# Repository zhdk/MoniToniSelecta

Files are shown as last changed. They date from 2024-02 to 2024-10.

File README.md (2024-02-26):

<h1>MoniToni Vending Machine Integration</h1>
Integration of ZHdK-Workshop Vending Machines into the MoniToni Payment System
<h2>Hardware</h2>
<h3>Electrical</h3>
<h3>Embedded Systems</h3>
Microcontroller: ESP32-S3 DevKitC by Esprssif <href>https://docs.espressif.com/projects/esp-idf/en/latest/esp32s3/hw-reference/esp32s3/user-guide-devkitc-1.html</href>
<h2>Setup</h2>
<h3>MAC-Address</h3>
Get specific MAC-Address of used ESP32-S3
<h3>WIFI</h3>
<h3>Hardware Tests</h3>
<h3>MoniToni-Terminal ID</h3>
<h3>TO-DO</h3>
<li>Generalized Item Amount</li>

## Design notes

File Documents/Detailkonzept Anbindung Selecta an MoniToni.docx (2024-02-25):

# Detailkonzept Anbindung Selecta an MoniToni

# 1. Ausbau der alten Komponenten

- Klimakompressor
- FL- Beleuchtung
- Kassensystem
- Printplatten
- Kühlaggregat
- Expansionsgefäss
- Ventilatoren
- Zahlterminal
- 10ner Tastatur
- Kassentresor
- Münzeinwurf

# 2. Einbau der Mechanischen und elektrischen Komponenten

## Einbau der elektronischen Steuereinheit im unteren Bereich der Türe und im Apparat, alle nicht genutzten Löcher werden verschlossen (Sicherheit)

- 1x Arduino mit WLAN
- 1x externe Antenne
- 2x Relaisboard (1x in der Türe, 1x im Automaten)
- 1x Schalter (Push) im Automaten (Befüllen)
- 1x Netzgerät 5V in der Türe (Arduino und Relaisboard
- 1x Netzgerät 24V in der Türe
- 1x USB-Ladegerät
- 2x 1.5m LED-Band für die Beleuchtung
- 1x Piezo (Fach- Summer, wenn Offen)
- 10x Grüne LED, wenn Ready zum Materialkauf (Türe entriegelt)
- 1x Relais für Motor
- 1x DIN-Schiene
- 1x Feinsicherung DIN-Schiene 5V (A unbekannt)
- 1x Feinsicherung DIN-Schiene 24V (A unbekannt)
- 1x Ventilator 5V oder 24V
- 1x Zuluftgitter
- 1x Apparatesteckdose

# 3. Beschriftung des Apparates und Funktionen

- Preise (pro Etage)
- QR-Code (pro Etage)
- Wahlselektor= Push&Hold

# 4. Funktion der Mechanik

- 1. Inhouse Schalter, um die Trommeln zu drehen (Befüllen)
- 2. Gelber Knopf Push -> Wakeup (Licht, Wlan connection Ja/Nein, Gelber Knopf leuchtet, wenn Gerät Ready)
- 3. Gelber Knopf Hold -> Produktewahl (alle Ebenen entsperren, Relais in Serie), Trommelmotor läuft nach 0.5 sec. Verzögerung zu den Relais)
- 4. Wenn gelber Knop losgelassen wird = Motor Stopp -> alle Ebenen sperren, Motor läuft 3 sec. weiter
- 5. QR von gewünschter Produktebene scannen -> wenn Kauf bewilligt wird, türfachfach der Ebene wird freigeschaltet, freigeschaltete Ebene wird optisch angezeigt (LED) Motor kann nicht gedreht werden.
- 6. Warenbezug -> Türe wird aufgeschoben, Schalter Zustand Türe offen (Summer (Delay 5 Sek.) ertönt so lange wie Türschalter offen, MoniToni wird abgerechnet)
- 7. Türe schliessen -> Türschalter schliesst, Summer stumm, Türe wird verriegelt
- Gerätestatus wie 3.
- 8. Sleep Mode -> nach 5 Minuten

# 5. Programmierung Arduino

## Input

- Gelber Knopf, aufwecken, Gelber Knopf gedrückt halten, Trommelrelais (in Serie) freischalten, nach 0.5 sec. Motorstart bis zum gewünschten Produkt, gelber Knopf loslassen, Relais stromlos (sperren), 3 sec. Motornachlaufachlauf
- Fächerschalter (in Serie)
- QR von gewünschter Produktebene scannen -> wenn Kauf bewilligt, Türfachfach der Ebene wird freigeschaltet, freigeschaltete Ebene wird optisch angezeigt (grün LED)
- Warenbezug -> Türe wird aufgeschoben, MoniToni wird abgerechnet) Schalter Zustand Türe offen Signal an Arduino (Summer Delay 5 Sek. ertönt so lange wie Türschalter offen,

## Output

- 1x Ebenen freischalten (Trommelrelais in Serie)
- Motor Steuerung
- 10x Fächerrelais steuern für den Verkauf
- LED-Beleuchtung
- Piezo (Summer)
- 10x grüne LED`s

# 6. Cubera

- Maschine erstellen
- Produkte erstellen
- Preise anpassen
- Auswertung jeder einzelnen Maschine (Geldfluss)

# 7. Test-Cases

- Systemtest Mechanisch
- Regressionstest ganzes MoniToni

# 8. Bestellliste für 4 Automaten

- 4x Arduino mit WLAN (Muss noch genau eruiert werden welches)
- 4x Externe Antenne
- 8x Relaisboard
- 4x Schalter (Pushbutton)
- 4x Netzgerät 5V
- 4x Netzgerät 24V
- 16m LED Band Beleuchtung
- 4x Piezo für offene Schublade
- 40x grüne LED für Schublade offen
- 4x Relais 24V/230V Motor
- 4x Apparatesteckdose 230V
- 4x 30cm DIN-Schiene für Elektroinstallationen
- 4x Feinsicherung DIN-Schiene 5V (A unbekannt)
- 4x Feinsicherung DIN-Schiene 24V (A unbekannt)
- Mehradriges Kabel
- 2x USB-Ladegerät
- 4x Ventilator 5V oder 24V
- 4x Zuluftgitter

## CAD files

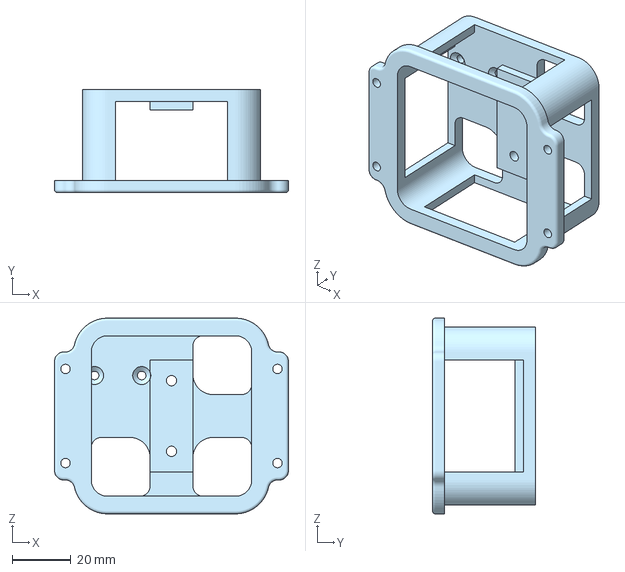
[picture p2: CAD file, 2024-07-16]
Hardware/3D-Print/M5CoreS3 Panel Front Mount Frame.3mf
79.5 x 35.0 x 66.5 mm

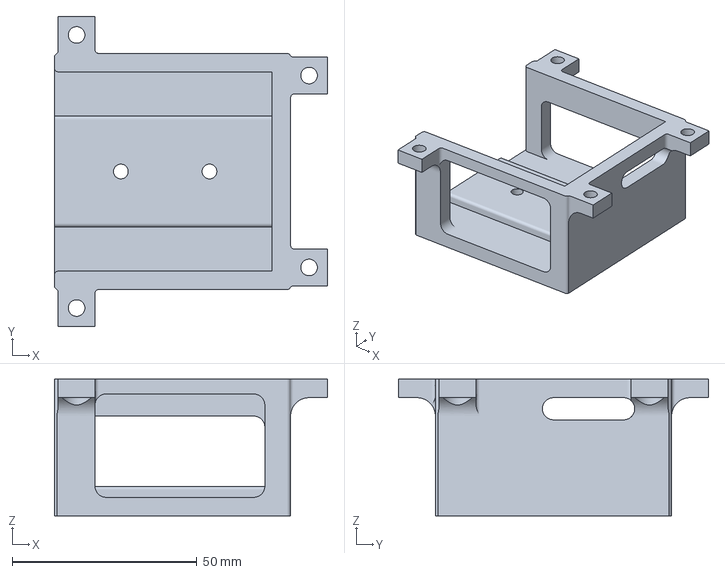
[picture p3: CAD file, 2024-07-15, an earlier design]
Hardware/3D-Print/Legacy/M5CoreS3 Mounting Frame.3mf
74.0 x 84.0 x 37.0 mm

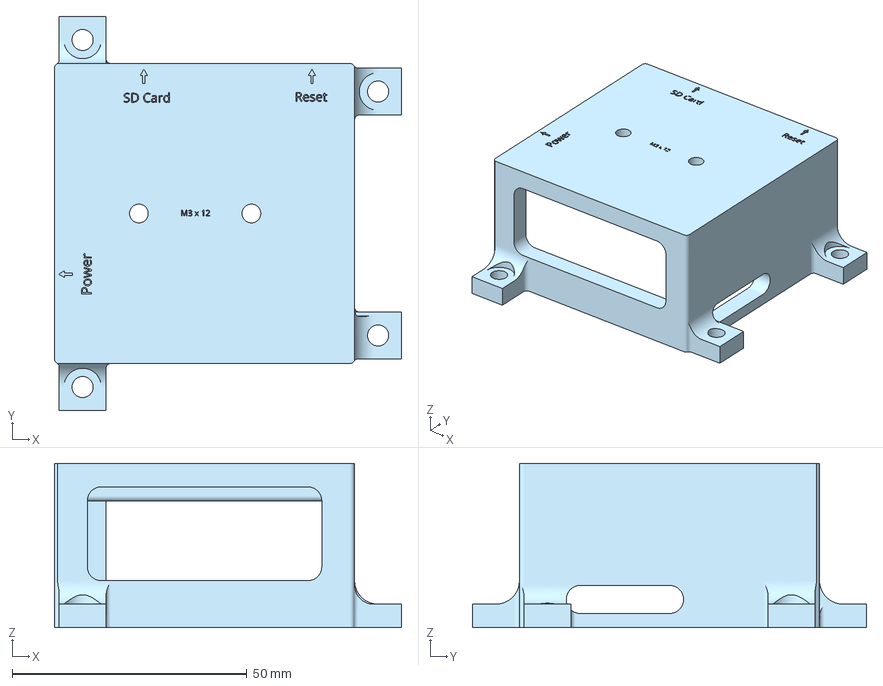
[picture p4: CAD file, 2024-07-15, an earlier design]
Hardware/3D-Print/Legacy/M5CoreS3 Mounting Frame - Display Offset.3mf
74.0 x 84.0 x 35.0 mm

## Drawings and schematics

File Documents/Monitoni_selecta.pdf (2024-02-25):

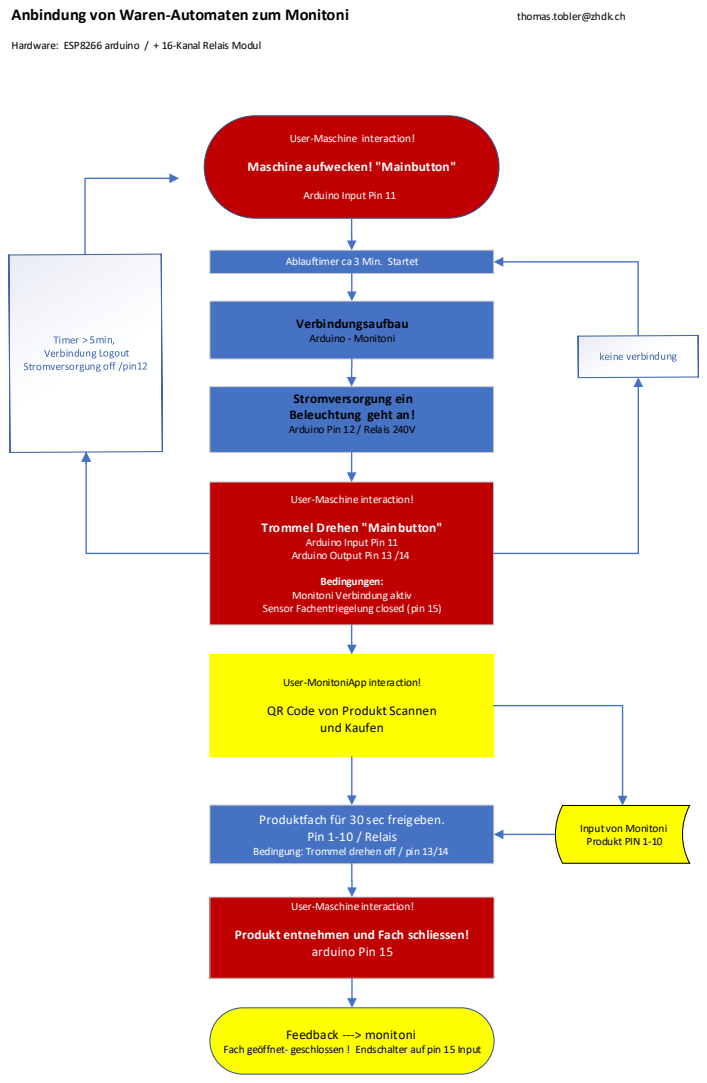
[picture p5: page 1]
Verbindungsaufbau Arduino - Monitoni; und Kaufen; Pin 1-10 / Relais; arduino Pin 15; Feedback ---> monitoni; Anbindung von Waren-Automaten zum Monitoni; thomas.tobler@zhdk.ch

Hardware: ESP8266 arduino / + 16-Kanal Relais Modul

User-Maschine interaction!

Maschine aufwecken! "Mainbutton"

Arduino Input Pin 11

Ablauftimer ca 3 Min. Startet

Stromversorgung ein
Beleuchtung geht an!
Arduino Pin 12 / Relais 240V

Trommel Drehen "Mainbutton"

Arduino Output Pin 13 /14

Bedingungen:
Monitoni Verbindung aktiv
Sensor Fachentriegelung closed (pin 15)

User-MonitoniApp interaction!

QR Code von Produkt Scannen

Produktfach für 30 sec freigeben.

Input von Monitoni
Produkt PIN 1-10

Bedingung: Trommel drehen off / pin 13/14

Produkt entnehmen und Fach schliessen!

Fach geöffnet- geschlossen ! Endschalter auf pin 15 Input

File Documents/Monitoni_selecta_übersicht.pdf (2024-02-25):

1)

## Selecta-

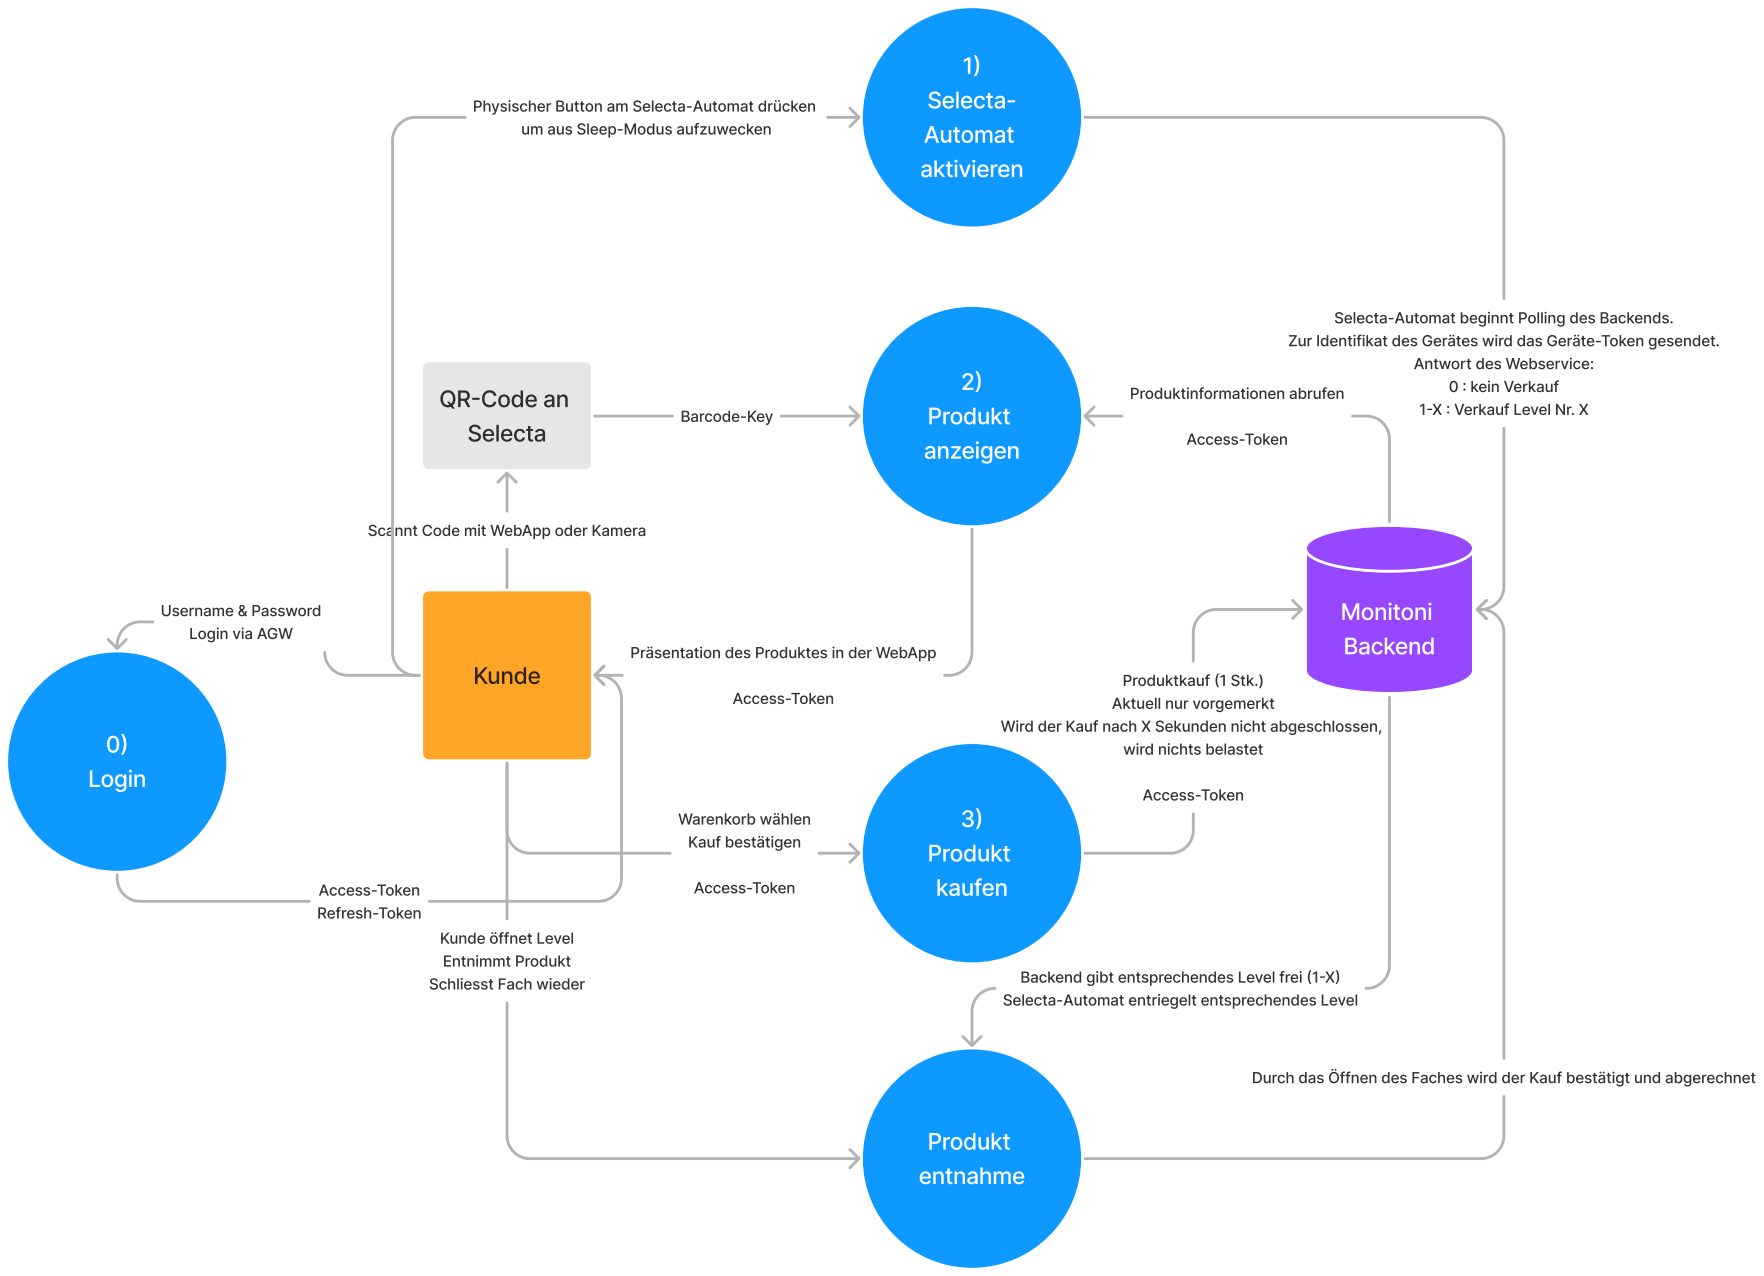
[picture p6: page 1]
Selecta; Produkt; anzeigen; Barcode-Key; Monitoni; Backend; Produktinformationen abrufen; Access-Token; Kunde; kaufen; Warenkorb wählen; Kauf bestätigen; Produktkauf (1 Stk.); Automat; aktivieren; 0 : kein Verkauf; entnahme; öffnet Leve l; Entnimmt Produkt; Schliesst; Fach wieder; Durch das; Öffnen des; Login; & Passwor d; Access-Toke n; Refresh-Token

Physischer Button am Selecta-Automat drücken

um aus Sleep-Modus aufzuwecken

Selecta-Automat beginnt Polling des Backends.

Zur Identifikat des Gerätes wird das Geräte-Token gesendet.

Antwort des Webservice:

QR-Code an

1-X : Verkauf Level Nr. X

Scannt Code mit WebApp oder Kamera

Username
Login via AGW

Präsentation des Produktes in der WebApp

Aktuell nur vorgemerkt

Wird der Kauf nach X Sekunden nicht abgeschlossen,

wird nichts belastet

Backend gibt entsprechendes Level frei (1-X)

Selecta-Automat entriegelt entsprechendes Level

Faches wird der Kauf bestätigt und abgerechnet

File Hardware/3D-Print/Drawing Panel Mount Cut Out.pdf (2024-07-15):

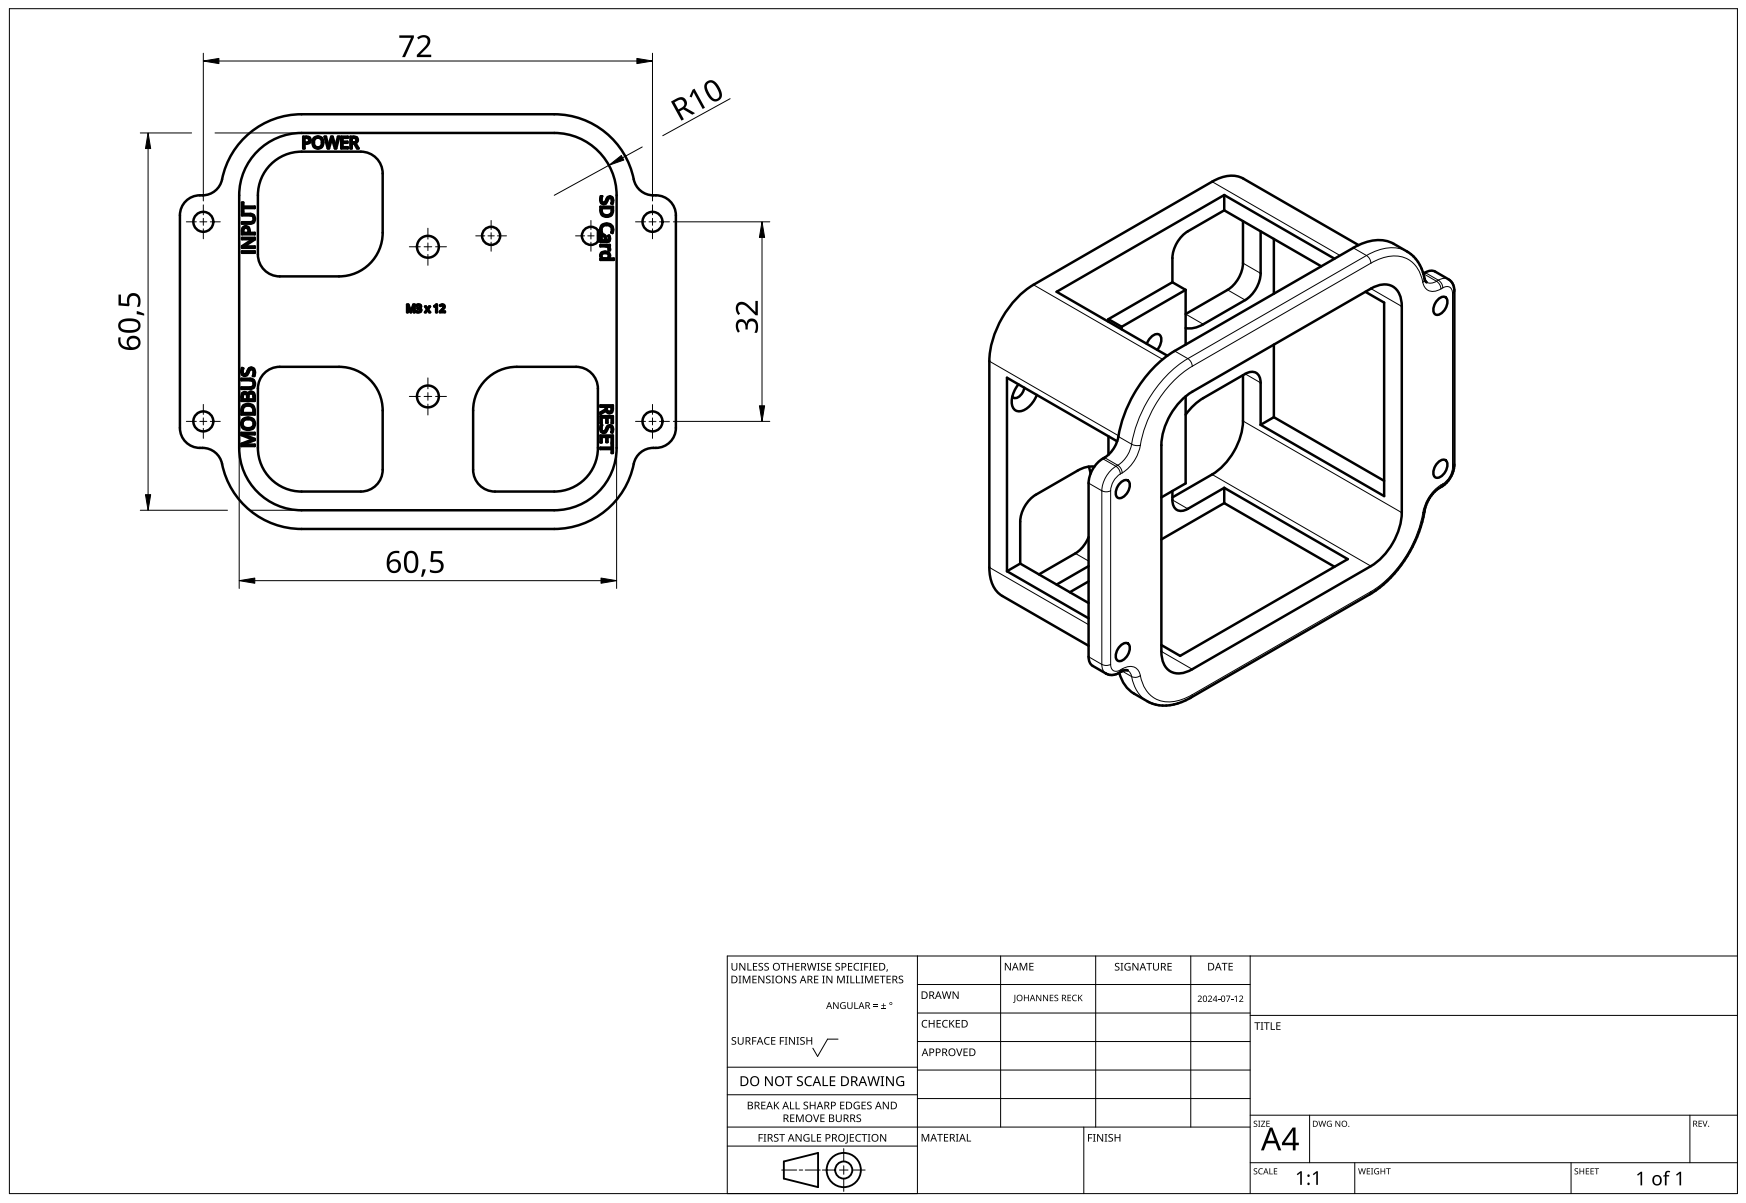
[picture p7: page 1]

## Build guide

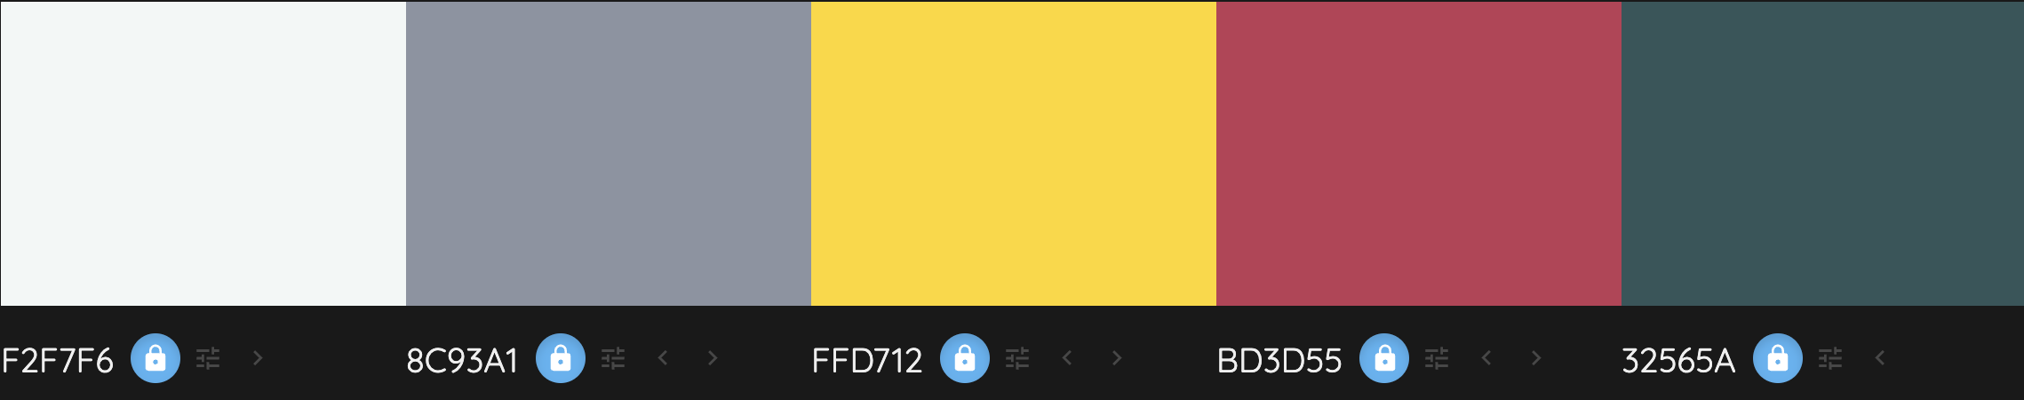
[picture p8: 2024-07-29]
UI/Color Guide/Illustrator/MoniToni Color Palette.png

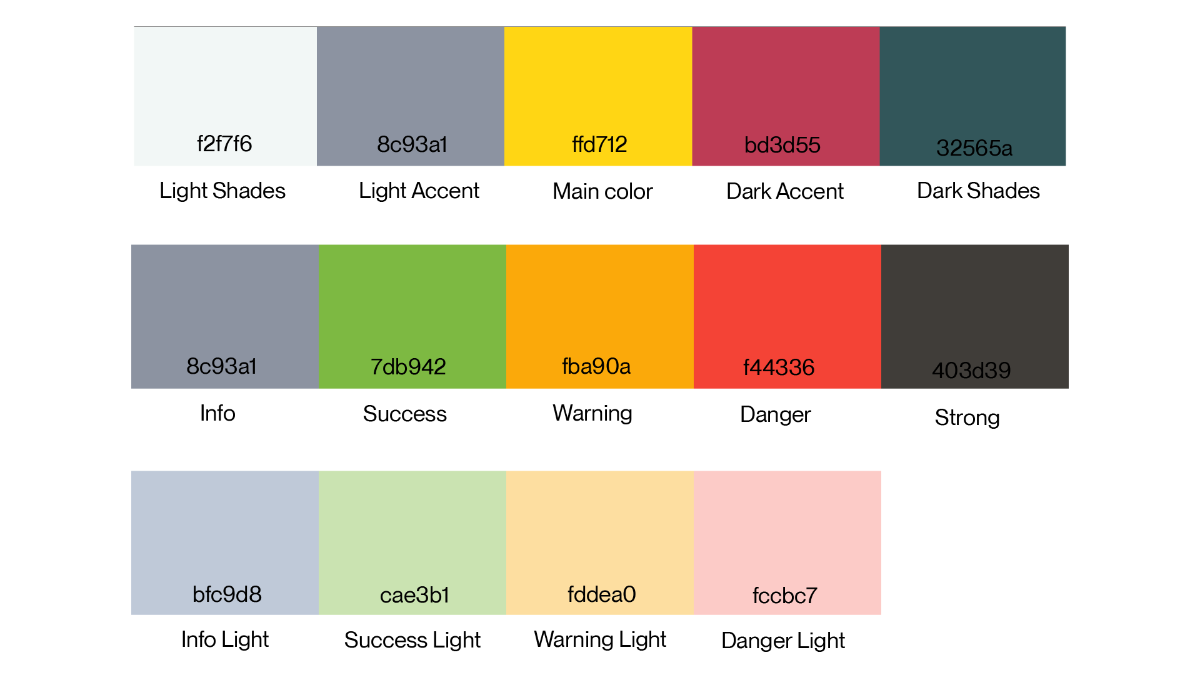
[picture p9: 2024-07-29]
UI/Color Guide/Codes.png

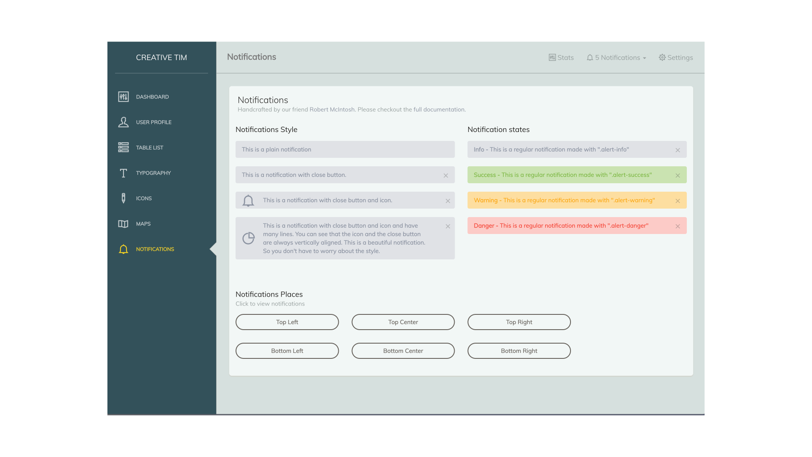
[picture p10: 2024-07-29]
UI/Color Guide/Example.png

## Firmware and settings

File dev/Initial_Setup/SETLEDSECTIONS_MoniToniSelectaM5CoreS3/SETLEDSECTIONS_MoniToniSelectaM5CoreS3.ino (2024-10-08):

// _____________MoniToni Vending Machine Integration_____________
// Hardware Iteration: M5CoreS3 Microcontroller & Waveshare 32CH Modbus RTU Relay Board



// _____________definitions_____________
// Debugger
// define DEBUGLOG_ENABLE_FILE_LOGGER to enable file logger
#define DEBUGLOG_ENABLE_FILE_LOGGER

// set log level NONE, ERROR, WARN, INFO, DEBUG, TRACE
#define DEBUGLOG_DEFAULT_LOG_LEVEL_DEBUG

// set log level for file output NONE, ERROR, WARN, INFO, DEBUG, TRACE
#define DEBUGLOG_DEFAULT_FILE_LEVEL_TRACE

// choose one of the two debug preambles
// default preamble with file & codeline information about debug source
//  #define LOG_PREAMBLE LOG_SHORT_FILENAME, LOG_MACRO_APPEND_STR(L.__LINE__), __func__, ":"
// no preamble
#define LOG_PREAMBLE ""

// Uncommenting DEBUGLOG_DISABLE_LOG disables ASSERT and all log (Release Mode)
// PRINT and PRINTLN are always valid even in Release Mode
// #define DEBUGLOG_DISABLE_LOG


// SD Card
#define SD_SPI_SCK_PIN  36
#define SD_SPI_MISO_PIN 35
#define SD_SPI_MOSI_PIN 37
#define SD_SPI_CS_PIN   4

// SERIAL2 PINS M5CoreS3
#define RX_PIN_SERIAL2 18
#define TX_PIN_SERIAL2 17

// PINS IN
// #define Door_PIN 8   //GPIO 8 - M5CoreS3
// #define ButtonTurn_PIN 48 
// #define ButtonOpen_PIN 21 

// RELAY CONFIG
#define Item_1_CH 1  //Relay 1
#define Item_2_CH 2  //Relay 2
#define Item_3_CH 3  //Relay 3
#define Item_4_CH 4  //Relay 4
#define Item_5_CH 5  //Relay 5
#define Item_6_CH 6  //Relay 6
#define Item_7_CH 7  //Relay 7
#define Item_8_CH 8  //Relay 8 
#define Item_9_CH 9  //Relay 9
#define Item_10_CH 10  //Relay 10
#define Light_CH 11  //Relay 11
#define Lock_CH 12  //Relay 12
#define Sirene_CH 13  //Relay 13
#define Motor_CH 14  //Relay 14
#define Relay15_CH 15  //Relay 15
#define Relay16_CH 16  //Relay 16
// #define Error_PIN 47 //Yellow


// Delays (in microseconds)
// #define CarrouselDELAY 100
#define CarrouselDELAY 0
#define UserInputDELAY 5000
#define SleepDELAY 120000
#define debounceTurnButton 1
#define debounceOpenButton 1
#define debounceDoor 10
#define openDoorDELAY 500
#define PurchaseTimeoutDELAY 60000
#define DoorOpenSireneDELAY 10000
#define ServerTimeout 3000
#define MotorTurnDELAY 2400
#define BluetoothSetupDelay 15000
#define ErrorDELAY 3000


// Proximity Sensor
#define ProximityThreshold 3


// Speaker Volume [0 - 255]
#define SpeakerVolume 60
// Speaker Frequency [in Hz]
#define SpeakerFrequency 1000


// Graphics
// Display Brightness [0 - 100]
#define TFT_BRIGHTNESS 90
// Screen Resolution
#define TFT_HOR_RES   240
#define TFT_VER_RES   320

/*LVGL draw into this buffer, 1/10 screen size usually works well. The size is in bytes*/
// #define DRAW_BUF_SIZE (TFT_HOR_RES * TFT_VER_RES / 10 * (LV_COLOR_DEPTH / 8))
#define DRAW_BUF_SIZE (TFT_HOR_RES * TFT_VER_RES / 8 * (LV_COLOR_DEPTH / 8))
//uint32_t draw_buf[DRAW_BUF_SIZE / 4];

#define READINGDELAY 8000

// LED Hub Port
#define CONNECTEDHUBPORT 0

// LED PIXEL COUNT
#define LED_PIN 9

// LED PIXEL COUNT
#define NUMPIXELS 172

// LED BRIGHTNESS [0 - 255]
#define BRIGHTNESS 255

// LED BLINKRATE
#define BLINKRATE 500

// LED MAPPING
#define LED_LEVEL_1_START 0
#define LED_LEVEL_1_END 17
#define LED_LEVEL_2_START 18
#define LED_LEVEL_2_END 34
#define LED_LEVEL_3_START 35
#define LED_LEVEL_3_END 51
#define LED_LEVEL_4_START 52
#define LED_LEVEL_4_END 68
#define LED_LEVEL_5_START 69
#define LED_LEVEL_5_END 85
#define LED_LEVEL_6_START 86
#define LED_LEVEL_6_END 103
#define LED_LEVEL_7_START 104
#define LED_LEVEL_7_END 120
#define LED_LEVEL_8_START 121
#define LED_LEVEL_8_END 137
#define LED_LEVEL_9_START 138
#define LED_LEVEL_9_END 154
#define LED_LEVEL_10_START 155
#define LED_LEVEL_10_END 172





// _____________Library Imports_____________

// M5CoreS3.h Libary by Tinyu-Zhao,M5Stack [1.0.0]
#include <M5CoreS3.h>

// Timer.h by Stefan Staub [1.2.1]
#include <Timer.h>

// ArduinoJson.h by Benoit Blanchon [7.0.3]
#include <ArduinoJson.h>

// SPI.h by Arduino [2.1.1] (Arduino IDE Version)
#include <SPI.h>

// WiFiClientSecure.h by Espressif Systems [2.0.11] (esp32 Boards Version)
#include <WiFiClientSecure.h>

// Wire.h for PBHUB I2C Communication
#include <Wire.h>

// debounce.h by Aaron Kimball [0.2.0]
#include <debounce.h>

// SD.h by Arduino, SparkFun [1.2.4]
#include <SD.h>

// DebugLog.h by hideakitai [0.8.3]
#include <DebugLog.h>

// Modbus Checksum Calculation
#include "modbus_crc.h"

// lvgl UI library [CUSTOM CONFIG & MODIFIED TFT_eSPI DRIVER]
#include <lvgl.h> 

// TFT display library [CUSTOM CONFIG]
#include <TFT_eSPI.h>

// UI Files [CUSTOM UI Files]
#include <ui.h>

// Credentials File
#include "credentials.h"

// // PBHUB Class
// #include "porthub.h"

// PBHUB, M5 [1.0.0]
#include <M5UnitPbHub.h>

#include <Adafruit_NeoPixel.h>

// _____________variables_____________

// Logic Variables
volatile int vendingState = 1; // 0 = Sleep, 1 = Idle, 2 = Turn, 3 = Validate, 4 = Collect, 5 = Finished, 6 = Error

volatile int activeScreen = 0; //  0 = StartUpScreen, 1 = MainScreen, 2 = ValidationScreen, 3 = EndScreen, 4 = SleepScreen, 5 = ErrorScreen

volatile int item;

volatile bool doorOpenState = false;
volatile bool buttonTurnPushedState = false;
volatile bool buttonOpenPushedState = false;
volatile bool carrouselUnlockedState = false;
volatile bool motorOnState = false;
volatile bool itemUnlockedState = false;
volatile bool sireneOnState = false;
volatile bool lightOnState = false;
volatile bool errorOnState = false;
volatile bool transactionActive = false;
volatile bool requestActive = false;
volatile bool proximityTriggered = false;
volatile bool displayOn = true;

// Network Variables
const char *SSID = WIFI_SSID;        // Change this to your WiFi SSID
const char *PW = WIFI_PASS; // Change this to your WiFi password
volatile bool wifiError = false;


const String host = "monitoni.zhdk.ch";
const int port = 443;

String url_permission = "/api/vending/permission";
String url_complete = "/api/vending/complete";
String url_close = "/api/vending/close";
String monitoni_terminal = TOKEN;

volatile bool permission = false;
volatile bool completed = false;
volatile bool closed = false;

volatile int globalHour;
volatile int globalMinute;
struct tm timeinfo;
time_t now;

void *draw_buf_1;                     // Draw Buffer for Graphics
unsigned long lastTickMillis = 0;   // Tick Variable for
lv_display_t * disp;                //display instance

uint16_t read_ps_value;   // Porximity Sensor Value

// PortHub porthub;  // PBHUB Instance
M5UnitPbHub pbhub;

// Pixel Instance - set number of LEDs, pin number, LED type.
Adafruit_NeoPixel LedPixels = Adafruit_NeoPixel(
    NUMPIXELS, LED_PIN,
    NEO_RGB + NEO_KHZ800);  


const int LEDMAPPING_LEVELS[10][2] = {
  {LED_LEVEL_1_START, LED_LEVEL_1_END},
  {LED_LEVEL_2_START, LED_LEVEL_2_END},
  {LED_LEVEL_3_START, LED_LEVEL_3_END},
  {LED_LEVEL_4_START, LED_LEVEL_4_END},
  {LED_LEVEL_5_START, LED_LEVEL_5_END},
  {LED_LEVEL_6_START, LED_LEVEL_6_END},
  {LED_LEVEL_7_START, LED_LEVEL_7_END},
  {LED_LEVEL_8_START, LED_LEVEL_8_END},
  {LED_LEVEL_9_START, LED_LEVEL_9_END},
  {LED_LEVEL_10_START, LED_LEVEL_10_END}
};

const int LED_COLORS[8][3] = {
  {0, 0, 0},    // OFF
  {0, 255, 0},  // GREEN
  {255, 0, 0},   // RED
  {0, 0, 255},    // BLUE
  {255, 255, 0},  // YELLOW
  {255, 0, 255},   // MAGENTA
  {0, 255, 255},    // CYAN
  {255, 255, 255}  // WHITE
};

volatile int previousTimeBlink = 0;
volatile bool blinkOn = false; 


// _____________instances_____________

WiFiClientSecure client;

Timer timerButtonTurnPress;
Timer timerButtonOpenPress;
Timer timerSleep;
Timer timerPurchaseTimeout;
Timer timerServerTimeout;
Timer timerDoorOpen;

Ltr5xx_Init_Basic_Para device_init_base_para = LTR5XX_BASE_PARA_CONFIG_DEFAULT;


static void doorSwitchHandler(uint8_t btnId, uint8_t btnState) {
  if (btnState == BTN_OPEN) {
    LOG_TRACE("LOGIC: doorOpenState set to true");
    doorOpenState = true;
    timerDoorOpen.stop();
    return;
  }

  // btnState == BTN_PRESSED.
  LOG_TRACE("LOGIC: doorOpenState set to false");
  doorOpenState = false;
  LOG_TRACE("TIMER: Door Open Timer started");
  timerDoorOpen.stop();
  timerDoorOpen.start();
}

static Button doorSwitch(1, doorSwitchHandler);




// _____________MODBUS Functions_____________

void sendModbusOpen(int relayNumber) {
  unsigned char relayNumberAddress = relayNumber - 1;
  unsigned char  cmdModbus[8] = {0x01,0x05,0,0,0,0,0,0}; 
  unsigned int   checksumModbus;
  unsigned char sendByteModbus;

  cmdModbus[2] = 0;
  cmdModbus[3] = relayNumberAddress;
  cmdModbus[4] = 0xFF;
  cmdModbus[5] = 0;
  checksumModbus = ModbusCRC((unsigned char  *)cmdModbus,6);
  cmdModbus[6] = checksumModbus & 0xFF;
  cmdModbus[7] = checksumModbus >> 8;
  for(sendByteModbus=0;sendByteModbus<8;sendByteModbus++){
    Serial2.write(cmdModbus[sendByteModbus]);
  }
  delay(100);
}

void sendModbusClose(int relayNumber) {
  unsigned char relayNumberAddress = relayNumber - 1;
  unsigned char  cmdModbus[8] = {0x01,0x05,0,0,0,0,0,0}; 
  unsigned int   checksumModbus;
  unsigned char sendByteModbus;

  cmdModbus[2] = 0;
  cmdModbus[3] = relayNumberAddress;
  cmdModbus[4] = 0;
  cmdModbus[5] = 0;
  checksumModbus = ModbusCRC((unsigned char  *)cmdModbus,6);
  cmdModbus[6] = checksumModbus & 0xFF;
  cmdModbus[7] = checksumModbus >> 8;
  for(sendByteModbus=0;sendByteModbus<8;sendByteModbus++){
    Serial2.write(cmdModbus[sendByteModbus]);
  }
  delay(100);
}

// select command to receive by setting argument cmd. 0 = receive address, 1 = receive baudrate, 
void receiveModbus(int cmd) {

}


// _____________Hardware Functions_____________

void carrouselLock()
{
  sendModbusClose(Lock_CH);
  LOG_TRACE("LOGIC: carrouselUnlockedState set to false");
  carrouselUnlockedState = false;
}

void carrouselUnlock()
{
  sendModbusOpen(Lock_CH);
  LOG_TRACE("HARDWARE: CarrouselDELAY");
  delay(CarrouselDELAY);
  LOG_TRACE("LOGIC: carrouselUnlockedState set to true");
  carrouselUnlockedState = true;
}


void motorOn()
{
  sendModbusOpen(Motor_CH);
  LOG_TRACE("LOGIC: motorOnState set to true");
  motorOnState = true;
}

void motorOff()
{
  sendModbusClose(Motor_CH);
  LOG_TRACE("LOGIC: motorOnState set to false");
  motorOnState = false;
}


void lightOn()
{
  LOG_DEBUG("HARDWARE: Light On deactivated!");
  // sendModbusOpen(Light_CH);
  // LOG_TRACE("LOGIC: lightOnState set to true");
  // lightOnState = true;
}

void lightOff()
{
  LOG_DEBUG("HARDWARE: Light Off deactivated!");
  // sendModbusClose(Light_CH);
  // LOG_TRACE("LOGIC: lightOnState set to false");
  // lightOnState = false;
}


void sireneOn()
{
  CoreS3.Speaker.tone(SpeakerFrequency);
  LOG_TRACE("LOGIC: sireneOnState set to true");
  sireneOnState = true;
}

void sireneOff()
{
  CoreS3.Speaker.stop();
  LOG_TRACE("LOGIC: sireneOnState set to false");
  sireneOnState = false;
}


void itemUnlock(int item)
{
  LOG_TRACE("LOGIC: itemUnlockedState set to true");
  itemUnlockedState = true;
  LOG_TRACE("HARDWARE: Solenoid ,", item, " triggered");
  sendModbusOpen(item);
}

void itemLock(int item)
{
  LOG_TRACE("LOGIC: itemUnlockedState set to false");
  itemUnlockedState = false;
  LOG_TRACE("HARDWARE: Solenoid ,", item, " released");
  sendModbusClose(item);
}



/////////////////////////////////////Based on system Setup included in main file
// static Button buttonTurnSwitch(0, buttonTurnSwitchHandler);
// static Button doorSwitch(1, doorSwitchHandler);
// static Button buttonOpenSwitch(3, buttonOpenSwitchHandler);


static void updateSwitchInputs() {
  // update() will call buttonHandler() if PIN transitions to a new state and stays there
  // for multiple reads over 25+ ms.
  if (vendingState == 4 || vendingState == 5) {
    int buttonSignal = pbhub.digitalRead(CONNECTEDHUBPORT, 0);
    doorSwitch.update(buttonSignal);
    return;
  }
  // buttonTurnSwitch.update(digitalRead(ButtonTurn_PIN));
  // buttonOpenSwitch.update(digitalRead(ButtonOpen_PIN));
}

static void updateProximity() {
  // update proximity sensor
  read_ps_value  = CoreS3.Ltr553.getPsValue();
  if (read_ps_value > ProximityThreshold) {
    proximityTriggered = true;
  }
  else {
    proximityTriggered = false;
  }
}

//base function to controll leds
static void ledStatic (int firstLED, int lastLED, int color) {
  if (color == 0) {
    lightOnState = false;
    LedPixels.clear();
    return;
  }
  else {
    lightOnState = true;
    LedPixels.setBrightness(BRIGHTNESS);
    LedPixels.fill(LedPixels.Color(LED_COLORS[color][0], LED_COLORS[color][1], LED_COLORS[color][2]), firstLED, lastLED - firstLED + 1);
  }
  LedPixels.show();
  // //_LEDSTATIC set LEDs in color from firstLED to lastLED with BRIGHTNESS
  // porthub.hub_wire_setBrightness(HUB_ADDR[CONNECTEDHUBPORT], BRIGHTNESS);
  // porthub.hub_wire_fill_color(HUB_ADDR[CONNECTEDHUBPORT], firstLED, lastLED - firstLED + 1, LED_COLORS[color][0], LED_COLORS[color][1], LED_COLORS[color][2]);
}

static void ledBlink (int firstLED, int lastLED, int color, int speed) {
  LOG_TRACE("LOGIC: ledBlink");
  Serial.println("blink function triggered");
  // blink leds using previousTimeBlink to keep track of time passed and speed in ms from firstLED to lastLED with BRIGHTNESS and color
  if (millis() - previousTimeBlink > speed) {
    if (!blinkOn) {
      ledStatic(firstLED, lastLED, color);
      blinkOn = true;
      Serial.println("blink on");
    }
    else {
      ledStatic(firstLED, lastLED, 0);
      blinkOn = false;
      Serial.println("blink off");
    }
    previousTimeBlink = millis();
    Serial.println("blink time reset");
  }
}

static void ledSetWhite () {
  //_LEDWHITE turn on all white
  ledStatic(0, NUMPIXELS - 1, 7);
  //lightOnState = true;
}

static void ledSetRed () {
  //_LEDRED turn on all red
  ledStatic(0, NUMPIXELS - 1, 2);
  //lightOnState = true;
}

static void ledOff () {
  //_LED turn all off
  ledStatic(0, NUMPIXELS - 1, 0);
  lightOnState = false;
}

static void ledItemGreen (int itemLED, bool blink) {
  if (blink) {
    ledBlink(LEDMAPPING_LEVELS[itemLED - 1][0], LEDMAPPING_LEVELS[itemLED - 1][1], 2, BLINKRATE);   //_LEDGREEN blink green on itemLED
    return;
  }
  else {
    ledStatic(LEDMAPPING_LEVELS[itemLED - 1][0], LEDMAPPING_LEVELS[itemLED - 1][1], 1);   //_LEDGREEN turn on green on itemLED
  } 
}


// _____________MoniToni-Server HTTP Requests Functions_____________

bool permissionRequest()
{ 
  if (!requestActive) {
    //timerServerTimeout.stop();
    //timerServerTimeout.start();
  }
  // Serial.print("Connecting to ");
  // Serial.println(host);
  if (!client.connect("monitoni.zhdk.ch", 443))
  {
    // Serial.println("Connection failed");
    LOG_ERROR("ERROR: Connection failed - permission request");
    //_GUI SERVER ERROR MESSAGE ON ENDSCREEN
    if (activeScreen != 3) {
      lv_screen_load(ui_EndScreen);
      activeScreen = 3;
    }
    lv_obj_add_flag(ui_DeniedTransactionLabel, LV_OBJ_FLAG_HIDDEN);
    lv_obj_remove_flag(ui_ErrorTransactionLabel, LV_OBJ_FLAG_HIDDEN);
    lv_obj_add_flag(ui_CompleteTransactionLabel, LV_OBJ_FLAG_HIDDEN);
    lv_obj_add_flag(ui_DeniedLabel, LV_OBJ_FLAG_HIDDEN);
    lv_obj_remove_flag(ui_ErrorLabel, LV_OBJ_FLAG_HIDDEN);
    lv_obj_add_flag(ui_ThankYouLabel, LV_OBJ_FLAG_HIDDEN);
    ui_ticker();
    lv_task_handler(); //_GUI ui handler
    CoreS3.delay(READINGDELAY); //_GUI READINGDELAY
    return 0;
  }

  // Send HTTP request
  // Serial.print("Requesting URL: ");
  // Serial.println(url_permission);
  client.println(String("GET " + url_permission + " HTTP/1.0"));
  client.println(String("Host: " + host));
  client.println(String(monitoni_terminal));
  client.println(String("Connection: close"));
  if (client.println() == 0)
  {
    // Serial.println(String("Failed to send request"));
    client.stop();
    LOG_ERROR("ERROR: Failed to send request");
    //_GUI SERVER ERROR MESSAGE ON ENDSCREEN
    if (activeScreen != 3) {
      lv_screen_load(ui_EndScreen);
      activeScreen = 3;
    }
    lv_obj_add_flag(ui_DeniedTransactionLabel, LV_OBJ_FLAG_HIDDEN);
    lv_obj_remove_flag(ui_ErrorTransactionLabel, LV_OBJ_FLAG_HIDDEN);
    lv_obj_add_flag(ui_CompleteTransactionLabel, LV_OBJ_FLAG_HIDDEN);
    lv_obj_add_flag(ui_DeniedLabel, LV_OBJ_FLAG_HIDDEN);
    lv_obj_remove_flag(ui_ErrorLabel, LV_OBJ_FLAG_HIDDEN);
    lv_obj_add_flag(ui_ThankYouLabel, LV_OBJ_FLAG_HIDDEN);
    ui_ticker();
    lv_task_handler(); //_GUI ui handler
    CoreS3.delay(READINGDELAY); //_GUI READINGDELAY
    return 0;
  }
  else
  {
    // Serial.println("Request sent");
  }

  // Check HTTP status
  char status[32] = {0};
  client.readBytesUntil('\r', status, sizeof(status));
  // It should be "HTTP/1.0 200 OK" or "HTTP/1.1 200 OK"
  if (strcmp(status + 9, "200 OK") != 0)
  {
    // Serial.print(String("Unexpected response: "));
    LOG_ERROR("Status: ", status);
    client.stop();
    LOG_ERROR("ERROR: Unexpected response");
    //_GUI SERVER ERROR MESSAGE ON ENDSCREEN
    if (activeScreen != 3) {
      lv_screen_load(ui_EndScreen);
      activeScreen = 3;
    }
    lv_obj_add_flag(ui_DeniedTransactionLabel, LV_OBJ_FLAG_HIDDEN);
    lv_obj_remove_flag(ui_ErrorTransactionLabel, LV_OBJ_FLAG_HIDDEN);
    lv_obj_add_flag(ui_CompleteTransactionLabel, LV_OBJ_FLAG_HIDDEN);
    lv_obj_add_flag(ui_DeniedLabel, LV_OBJ_FLAG_HIDDEN);
    lv_obj_remove_flag(ui_ErrorLabel, LV_OBJ_FLAG_HIDDEN);
    lv_obj_add_flag(ui_ThankYouLabel, LV_OBJ_FLAG_HIDDEN);
    ui_ticker();
    lv_task_handler(); //_GUI ui handler
    CoreS3.delay(READINGDELAY); //_GUI READINGDELAY
    return 0;
  }

  // Skip HTTP headers
  char endOfHeaders[] = "\r\n\r\n";
  if (!client.find(endOfHeaders))
  {
    Serial.println(String("Invalid response"));
    client.stop();
    //_GUI SERVER ERROR MESSAGE ON ENDSCREEN
    if (activeScreen != 3) {
      lv_screen_load(ui_EndScreen);
      activeScreen = 3;
    }
    lv_obj_add_flag(ui_DeniedTransactionLabel, LV_OBJ_FLAG_HIDDEN);
    lv_obj_remove_flag(ui_ErrorTransactionLabel, LV_OBJ_FLAG_HIDDEN);
    lv_obj_add_flag(ui_CompleteTransactionLabel, LV_OBJ_FLAG_HIDDEN);
    lv_obj_add_flag(ui_DeniedLabel, LV_OBJ_FLAG_HIDDEN);
    lv_obj_remove_flag(ui_ErrorLabel, LV_OBJ_FLAG_HIDDEN);
    lv_obj_add_flag(ui_ThankYouLabel, LV_OBJ_FLAG_HIDDEN);
    ui_ticker();
    lv_task_handler(); //_GUI ui handler
    CoreS3.delay(READINGDELAY); //_GUI READINGDELAY
    LOG_ERROR("ERROR: Invalid response");
    return 0; 
  }

  // Allocate the JSON document
  // Use https://arduinojson.org/v6/assistant to compute the capacity.
  const size_t capacity = JSON_OBJECT_SIZE(1) + JSON_ARRAY_SIZE(2) + 60;
  DynamicJsonDocument doc(capacity);

  // Parse JSON object
  DeserializationError error = deserializeJson(doc, client);
  if (error)
  {
    Serial.print(String("deserializeJson() failed: "));
    Serial.println(error.f_str());
    client.stop();
    LOG_ERROR("ERROR: Deserialization failed");
    //_GUI SERVER ERROR MESSAGE ON ENDSCREEN
    if (activeScreen != 3) {
      lv_screen_load(ui_EndScreen);
      activeScreen = 3;
    }
    lv_obj_add_flag(ui_DeniedTransactionLabel, LV_OBJ_FLAG_HIDDEN);
    lv_obj_remove_flag(ui_ErrorTransactionLabel, LV_OBJ_FLAG_HIDDEN);
    lv_obj_add_flag(ui_CompleteTransactionLabel, LV_OBJ_FLAG_HIDDEN);
    lv_obj_add_flag(ui_DeniedLabel, LV_OBJ_FLAG_HIDDEN);
    lv_obj_remove_flag(ui_ErrorLabel, LV_OBJ_FLAG_HIDDEN);
    lv_obj_add_flag(ui_ThankYouLabel, LV_OBJ_FLAG_HIDDEN);
    ui_ticker();
    lv_task_handler(); //_GUI ui handler
    CoreS3.delay(READINGDELAY); //_GUI READINGDELAY
    return 0;
  }

  // Extract Values
  permission = doc["HasPermission"].as<bool>();

  if (permission == true)
  {
    transactionActive = true;
    timerServerTimeout.stop(); 
    //timerPurchaseTimeout.stop();
    //timerPurchaseTimeout.start();
    Serial.println(F("Item:"));
    Serial.println(doc["Item"].as<int>());
    item = doc["Item"].as<int>();
    // Disconnect
    client.stop();
    return 1;
  }
  else {
    transactionActive = false;
    //timerPurchaseTimeout.stop();
    // Disconnect
    client.stop();
    LOG_INFO("INFO: No Permission");
    return 0;
  }
}

///////////////////////------ complete request ------///////////////////////
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
void loop()
{
  CoreS3.update();
  // ledItemGreen(1,0);
  ledBlink(0, 200, 2, 500); 
  // for(int i = 0; i <= 10; i++) {
  //   ledItemGreen(i, 0);
  //   delay(2000);
  //   ledOff();
  // }
  // mainLoop();
}

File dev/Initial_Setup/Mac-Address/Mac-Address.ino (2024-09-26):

// Complete Instructions to Get and Change ESP MAC Address: https://RandomNerdTutorials.com/get-change-esp32-esp8266-mac-address-arduino/

// #ifdef ESP32
  #include <WiFi.h>
// #else
//   #include <ESP8266WiFi.h>
// #endif


void setup(){
  Serial.begin(115200);
  Serial.println();
  Serial.print("ESP Board MAC Address:  ");
  Serial.println(WiFi.macAddress());
}
 
void loop(){
  Serial.println(WiFi.macAddress());

}

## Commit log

2024-06-27 m5stack core 2 modbus waveshare relay 32 CH tests
2024-06-28 bambu print file
    [M5CoreS3 Mounting Frame.3mf]
2024-07-10 Hardware Tests & new 3d print
    [M5CoreS3 Mounting Frame - Display Offset.3mf]
2024-07-11 3d print - labeling
    [M5CoreS3 Mounting Frame - Display Offset.3mf]
2024-07-14 front panel mount holder
    [M5CoreS3 Panel Front Mount Frame.3mf]
2024-07-15 Adapt Mounting Frame
    [M5CoreS3 Mounting Frame - Display Offset.3mf, M5CoreS3 Mounting Frame.3mf, M5CoreS3 Panel Front Mount Frame.3mf]
2024-07-16 LVGL Touch Input Device Setup
    [M5CoreS3 Panel Front Mount Frame.3mf]
2024-07-18 lvgl display rotation & touch input device setup, lvgl styling
2024-07-20 button callbacks & ui_util
2024-07-21 modiefied libs
    [Configuring options.txt]
2024-07-28 performance improvements for harware updates of switch and proximity sensor
2024-07-29 UI Redesign & Hardware Functions for LED Strip implementation
    [MoniToniSelectaM5CoreS3.ino]
2024-07-29 fix LED_LEVELS & LED_COLORS definition
    [MoniToniSelectaM5CoreS3.ino]
2024-07-29 fixing ui flow
2024-08-04 led logic implementation
2024-08-06 ledstrip functions
2024-08-15 PBHUB config & LED implementation
2024-08-15 Tested w/ Slot 1 in Loki
2024-09-11 logic for blinking collect state fixed (repeated function call leading to strobing led)
    [Mac-Address.ino, MoniToniSelectaM5CoreS3.ino]
2024-09-11 adjust green item led blink speed
2024-09-12 Test for PBHub use as Door Switch
2024-09-12 Change Led Strip on PortB and Door Switch on PBHub
2024-09-26 adjusted LED Mapping for new mounting profile
